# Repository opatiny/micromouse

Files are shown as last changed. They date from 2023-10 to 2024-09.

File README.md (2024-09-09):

# Algernon: A custom micromouse robot

YouTube demo of the project: https://youtu.be/nz4QlaSIkbY

Main repository for my bachelor's thesis project.

wholeMouse

## Related repositories

The software fo this robot can be found in the two following repositories:

- Software for the microcontroller: [opatiny/ms-software](https://github.com/opatiny/ms-software)
- TypeScript code for the debug web page (is then built and uploaded on the MCU): [opatiny/ms-webpage](https://github.com/opatiny/ms-webpage)

## Abstract

This project was inspired by the micromouse competitions, in which small autonomous maze-solving robots compete to solve an unknown maze in the shortest possible time. The main focus of the project was to design a micromouse from scratch, which implied electrical and mechanical design, as well as the manufacturing of our own custom PCB. A physical prototype of the robot was fully assembled and tested. The robot implements 5 ToF distance sensors, an accelerometer and two brushed DC motors with encoders. The microcontroller is an ESP32-S3, and a 2P1S LiPo battery is used as a power supply. On the software side, all of the sensors were tested independently and are functional. A basic odometry task was also implemented, which allows to track the robot's position, and speed regulation of the wheels was added. What is more, a remote debug interface using WiFi was programmed in order to visualize the robot's status in real time.

## Report of the project

The report of this thesis can be found in the `docs` folder of this repository: [bachelor-thesis-opatiny.pdf](./docs/bachelor-thesis-opatiny.pdf)

## Repository structure

These are the main folders in this repository:

- `docs`: All sorts of documentation about the project, as well as the datasheets and useful images of the components used.
- `electronics`: Contains all the KiCad files of the PCB.
- `mechanics`: All files related to mechanical design and manufacturing. Also contains all of our custom maze files.
- `matlab`: Calculations and plot realized during the project.
- `software`: Not the actual micro-controller software. This only contains a few tests done using the Micromouse Simulator tool.

## Software

All the software of the robot is in its own repository: [opatiny/ms-software](https://github.com/opatiny/micromouse).

## Electronic design

The robot's PCB was fully designed in KiCad. The list of all the components used can be found in [docs/electronics/mouseHardware.md](./docs/electronics/mouseHardware.md).

Render of the final PCB
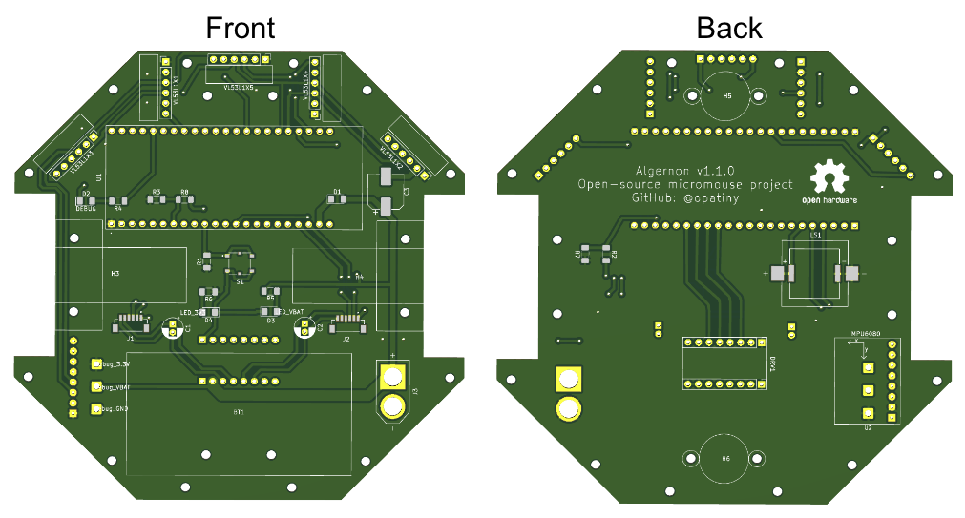
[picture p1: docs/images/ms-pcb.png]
pcb


3D view of the completed robot
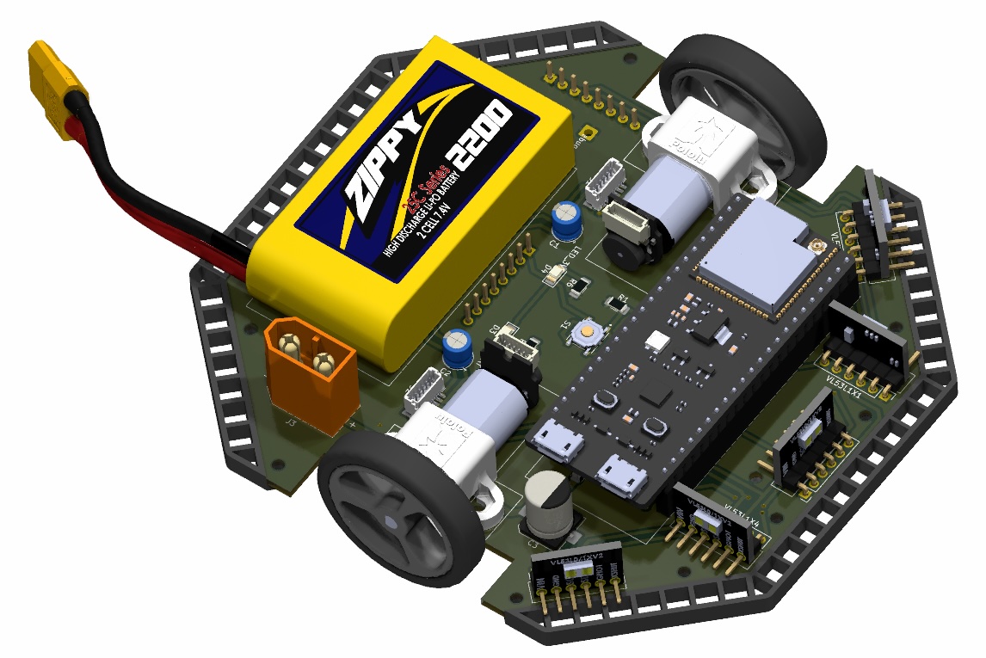
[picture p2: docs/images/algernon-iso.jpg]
3D


## Mechanical design

The mechanical design is relatively simple since the PCB is the main structural element. We just had to design our own caster wheel, that are 3D printed out of PETG, and custom bumpers, 3D printed out of flexible filament.

Comparison of commercial and custom caster wheel
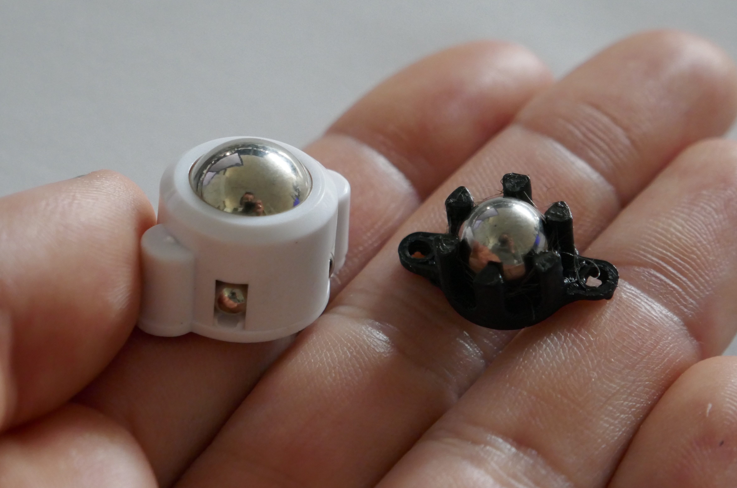
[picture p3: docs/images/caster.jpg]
caster


Close-up of the bumper
bumper

## Custom maze

In order to test our robot, we designed our own maze. The walls are 3mm MDF, spray painted white. The connectors are 3D printed out of PETG. Additional "bridge" parts are use to ensure the walls are parallel, and at the right distance from each other. All the parts were designed in solidworks.

The four types of connectors
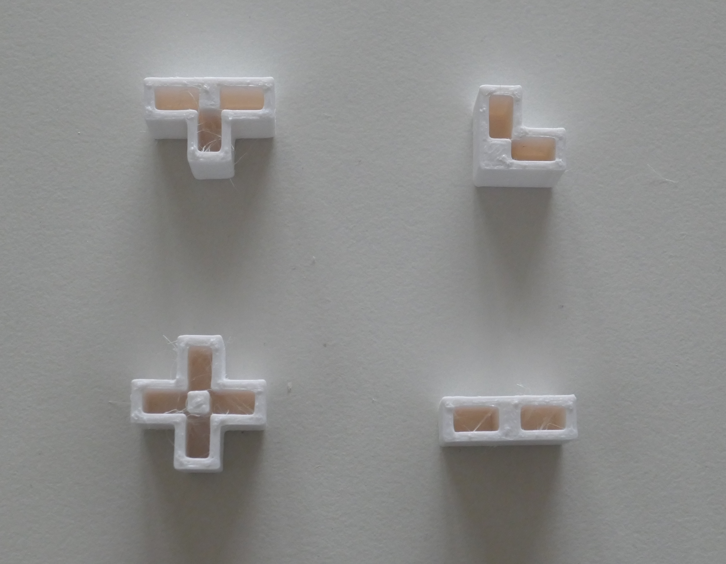
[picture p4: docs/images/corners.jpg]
connector


Example of a small section of maze, integrating one of the "bridge" parts
maze
bridge

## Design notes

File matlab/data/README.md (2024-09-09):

# Information about the data csv files

Motor speed absolute value from 0 to 255.

## Battery voltage when motors speed varies quickly

### `batteryVoltage1.csv`

- motor: 1
- motor speed: 200
- profile: rectangle
- length: 1 s
- sampling: 20 ms
- task priority: 0
- battery: 3S AAA batteries

### `batteryVoltage2.csv`

- motor: 1
- motor speed: 200
- profile: rectangle
- length: 1 s
- sampling: 5 ms
- task priority: 0
- battery: 3S AAA batteries

### `batteryVoltage3.csv`

- motor: 1
- motor speed: 200
- profile: rectangle
- length: 1 s
- sampling: 1 ms
- task priority: 2
- battery: 3S AAA batteries

### `batteryVoltage4.csv`

- motor: 1
- motor speed: 200
- profile: rectangle
- length: 1 s
- sampling: 5 ms
- task priority: 2
- battery: 3S AAA batteries

### `batteryVoltage4.csv`

- motor: 1
- motor speed: 100
- profile: rectangle
- length: 1 s
- sampling: 5 ms
- task priority: 2
- battery: LiPo battery 2S1P
- added 0.1uF ceramic capacitors on motor terminals

## Analyse distance sensors results

### `distanceSensorsConstant1.csv`

Using breadboard with 2 sensors to see what the measurements look like.

- constant distance of 250 mm from edge of board
- measurements every second using N times DELAY
- timing budget: 140 ms

### `distanceSensorsCalibration1.csv`

Using breadboard with 2 sensors to see what the measurements look like when distance varied.

- distance varied from 0 to 450 mm with 50mm steps (from edge of board)
- using the push button to measure when required
- timing budget: 140 ms

## Analyse encoders data

Log the data the encoder for a given speed profile. All measurements were made on motor 1.

### `encoders1.csv`

- profile: rectangle
- max speed: 100
- movement length: 1 s
- encoding: X4
- sampling: 5 ms

### `encoders2.csv`

- profile: trapeze
- ramp delay: 1
- max speed: 100
- movement length: 1 s
- encoding: X4
- sampling: 5 ms

### `encoders3.csv`

- profile: step response
- max speed: 100
- encoding: X4
- sampling: 5 ms

### `encoders4.csv`

- profile: trapeze
- ramp delay: 5
- max speed: 100
- movement length: 1 s
- encoding: X4
- sampling: 5 ms

### `encoders5.csv`

- profile: step response
- max speed: 255
- encoding: X4
- sampling: 5 ms

### `encoders6.csv`

- profile: trapeze
- ramp delay: 10
- max speed: 100
- movement length: 1 s
- encoding: X4
- sampling: 5 ms

## True wheel speed vs command

We want to analyse what the true wheel speed is depending on the duty cycle applied to the motor

- command (duty cycle) is a value between -256 and 255
- the actual motors speed is in rpm
- robot: Algernon v1.1.0
- motors 3 (left) and 4 (right)
- battery: LiPo battery 2S1P

### `wheelSpeedCalibration1.csv`

- delay between speed changes: 1s
- speed range: [0, 255]
- command step: 10

### `wheelSpeedCalibration2.csv`

- delay between speed changes: 2s
- speed range: [-255, 255]
- command step: 5

### `wheelSpeedCalibration3.csv`

- delay between speed changes: 1s
- speed range: [-255, 255]
- command step: 1

### `wheelSpeedCalibration5.csv`

- delay between speed changes: 1s
- speed range: [-255, 255]
- command step: 5

Caution: in this case we use the new speed measurement X/dt and the odometry delay is 1ms

## Wheel speed calibration

We use the same dataset types as for wheel speed calibration.

Check whether cpp and matlab yield to same result.

- command (duty cycle) is a value between -256 and 255
- robot: Algernon v1.1.0
- motors 3 (left) and 4 (right)
- battery: LiPo battery 2S1P

### `wheelSpeedCalibration4.csv` and `polynoms4.csv`

- delay between speed changes: 1s
- speed range: [-255, 255]
- command step: 5

### `wheelSpeedCalibration6.csv` and `polynoms6.csv`

- delay between speed changes: 1s
- speed range: [-255, 255]
- command step: 5

Caution: in this case we use the new speed measurement X/dt and the odometry delay is 1ms

## Test speed calibration

Verify if desired RPM speed and actual motor speed is the same.

- speed range: -550 -> 550 rpm
- robot: Algernon v1.1.0
- motors 3 (left) and 4 (right)
- battery: LiPo battery 2S1P

### `testSpeedCalibration1.csv`

- delay between speed changes: 1s
- speed step: 10 rpm

## Test PID

Check how the desired speed is reached by both wheels, using a PID regulator

- robot: Algernon v1.1.0
- motors 3 (left) and 4 (right)
- battery: LiPo battery 2S1P

## `testPid1.csv`

- Kp: 0.020
- Ki: 0.000
- Kd: 0.010

Time in ms.

## `testPid2.csv`

Completely refactored odometry to fix speed issues. Odometry and PID loops have a delay of 10 ms.

- Kp: 0.020
- Ki: 0.001
- Kd: 0.000

Time in seconds.

## `testPid3.csv`

- Kp: 0.020
- Ki: 0.000
- Kd: 0.001

Time in seconds.

## `testPid3.csv`

- Kp: 0.020
- Ki: 0.002
- Kd: 0.000

Time in seconds.

## `testPid6.csv`

- Kp: 0.015
- Ki: 0.003
- Kd: 0.000

## `testPid7.csv`

- Kp: 0.060
- Ki: 0.001
- Kd: 0.000

## Compare speed measurement methods

We measure the speed in 2 ways:

1. divide number of counts from since last call by the time elapsed
2. divide a known number of counts, always the same, by the time taken to move this nb of steps

- robot: Algernon v1.1.0
- motors 3 (left) and 4 (right)
- battery: LiPo battery 2S1P

### `compareSpeeds1.csv`

- odometry task delay: 10ms

```csv
 pNegLeft, pPosLeft, pNegRight, pPosRight
-0.0000000061, -0.0000000037, -0.0000000037, 0.0000000016
-0.0000052032, 0.0000054147, -0.0000028143, -0.0000009649
-0.0016165279, -0.0019280235, -0.0008025189, 0.0002857632
-0.0617476981, 0.2247056010, 0.0270471843, 0.0791166413
-42.7075095500, 74.9729712389, -45.3625414581, 45.1797983120
```

### `compareSpeeds2.csv`

- odometry task delay: 1ms
- same regressions as before
- we see that the speed speed is really big for smaller speeds: variations of 167 rpm at a time

Questions:

- why is the low speed never zero??

```csv
 pNegLeft, pPosLeft, pNegRight, pPosRight
-0.0000000061, -0.0000000037, -0.0000000037, 0.0000000016
-0.0000052032, 0.0000054147, -0.0000028143, -0.0000009649
-0.0016165279, -0.0019280235, -0.0008025189, 0.0002857632
-0.0617476981, 0.2247056010, 0.0270471843, 0.0791166413
-42.7075095500, 74.9729712389, -45.3625414581, 45.1797983120
```

### `compareSpeeds4.csv`

- odometry task delay: 1ms
- logging delay: 250 ms
- both high speed and low speed are computed every 1ms

## Controller delay impact

We have a delay in the `robotDriveStraight` function, that implements the speed controllers of the wheels. We vary this delay in order to see the impact on the step response of the controller. Ideally, we want to reduce this delay to the maximum, because delay in regulation loops lead to higher instability of the system.

- target speed: 200 rpm
- robot: Algernon v1.1.0
- motors 3 (left)
- battery: LiPo battery 2S1P

Files: `controllerDelayImpactXXms.csv`

## Analyse commands

Goal: see how much the command is increased over time in order to achieve desired speed in givn time.

## Max robot acceleration

Measuring the true maximal acceleration of the robot.

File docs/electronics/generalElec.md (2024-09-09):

# Components and features of the PCB

What do we want on our mouse?

- 2x DC motors with encoders
- 1x H bridge dual motor driver
- 1x MPU with bluetooth and/or wifi for debug
- 1x buzzer for sound signals
- debug LEDS
- 5x distance sensors
- battery
- accelerometer

The following sections include information on how the different elements work, and how we implemented them on the PCB. The list of the exact components used can be found in [mouseHardware.md](./mouseHardware.md).

## Distance sensors: VL53L1X

The device pins have the following functions:
[!](../datasheets/images/vl53l1x-pin-description.png)

- The `XSHUT` pin has to be pulled up for the device to be active.
- Device default address is 0x29 (41)
- Arduino library: Adafruit VL53L1X
- range: ~30 to 4000 mm -> the smallest distance is not great for our use case...
- timing budget: from 20 to 1000ms. Be careful, if the timing budget is too short, the whole MCU reboots. It basically defines how long a measurement can be.
  "140 ms is the timing budget which allows the maximum distance of 4 m (in the dark on a white chart) to be reached under Long distance mode Increasing the timing budget increases the maximum distance the device can range and improves the repeatability error. However, average power consumption augments accordingly." - https://xod.io/
- We can't change the I2C addresses permanently on the VL53L1X!!! https://community.st.com/t5/mems-sensors/vl53l1x-device-address-storage/td-p/355584
- we'll therefore need an I2C to GPIO module because otherwise we don't have enough pins on our MCU

- minimum timing budget: https://forum.pololu.com/t/vl53l1x-minimum-timing-budget/20485

## Buzzer

We'll need PWM to get different notes with the buzzer.
"All GPIO pins on XIAO ESP32S3 support PWM output. Therefore, you can use any pin to output PWM to adjust the brightness of lights, control servos, and other functions." - https://wiki.seeedstudio.com/xiao_esp32s3_pin_multiplexing/

The buzzer takes a frequency of typically 400kHz, how do we generate this? This is actually not true. You apply the frequency that you want to hear, so i.e. 440 Hz.

## Debug LEDs

We want to put a bunch of debug LEDs in the circuit.

- high power (from battery)
- 3.3V at voltage regulator output

## Battery voltage measurement

We want to add a voltage divider on the battery in order to measure the battery voltage and hence know when the battery is discharged. This requires reading an analog voltage -> ADC.

## Encoders

- we use an interrupt with a small routine that increases/decreases a counter depending on the spin direction

## Access ESP USB connector

Since it's very compact, we need USB angled connectors.

The connectors we bought are 18 x 13 x 7 mm.

## Final PCB v1.0.0

Dimensions: 110x110mm

Possible issues:

- add capas to decouple power lines near to important components (MCU, sensors)
- are we using the USB pins as GPIO and they would need to be reconfigured?
- do the murata buzzers work as expected?

## Links

- adafruit guide: https://learn.adafruit.com/adafruit-vl53l1x?view=all
- https://github.com/pololu/vl53l1x-arduino?utm_source=platformio&utm_medium=piohome
- timing budget reference: https://xod.io/libs/wayland/vl53l1x-time-of-flight/set-measurement-timing-budget/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,ms%20up%20to%201000%20ms.&text=20%20ms%20is%20the%20minimum,only%20in%20Short%20distance%20mode.&text=33%20ms%20is%20the%20minimum,work%20for%20all%20distance%20modes.

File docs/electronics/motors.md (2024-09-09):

# Motors and encoders

We are using brushed DC motors with an integrated gearbox. Additionally, we measure the motors movement with magnetic encoders.

## Voltage drop due to motors

"One major drawback to working with motors is the large amounts of electrical noise they produce. This noise can interfere with your sensors and can even impair your microcontroller by causing voltage dips on your regulated power line. Large enough voltage dips can corrupt the data in microcontroller registers or cause the microcontroller to reset." - https://www.pololu.com/docs/0J15/9

**Solution:** Solder 0.1uF ceramic capacitors (not polarized!) between motor terminals and motor case

## Cables

The Polulu motors encoders are equipped with JST SH cables. Two of the 6 pins are directly connected to the motors pins. By checking the specifications, we wee that the cables are 28AWG, which can have a maximal continuous current of 1.5A.

- http://www.mosaic-industries.com/embedded-systems/electronic-instrument-design-new-product-development/cables/ribbon-cable-current-rating
- https://www.pololu.com/product/4763/specs

## Non-linear motor speed VS PWM command

Is probably caused by the driver!! Other people had very similar results

- https://forum.pololu.com/t/nonlinear-relatioonship-between-motor-encoder-speed-and-pwm/20092/7
- change the PWM frequency!!! https://forum.pololu.com/t/drv8835-non-linear-current-draw-vs-pwm-duty-cycle/8430/4 -> around 20kHz

- could also be improved by using either coast mode (fast decay) or brake mode (slow decay). According to the previous link, brake mode would be the best. See the drivers datasheet (page 9) for how to use one mode or the other.

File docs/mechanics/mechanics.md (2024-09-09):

# Mechanical parts of the micromouse

## PCB: The main structural element

## Custom caster wheels

- M2 screw head between 3.3 and 3.5mm

- these caster wheels by polulu would have worked, they're only 10mm high: https://www.pololu.com/product/951

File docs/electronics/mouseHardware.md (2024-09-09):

# Algernon: The hardware

## Micro-controller

- Reference: ESP32-S3-DevKitC-1U-N8R8
- Manufacturer: Espressif
- Flash: 8 Mb
- RAM: 8 Mb
- CPU frequency: up to 240MHz
- SPI clock frequency: max 80 MHz by default
- Wireless: WiFi and Bluetooth
- Board dimensions: 63 x 25 mm
- Link: https://www.mouser.de/ProductDetail/356-32S3DEVKTC1UN8R8

## Motors

- Reference: 30:1 Micro Metal Gearmotor HPCB 12V with Extended Motor Shaft
- Manufacturer: Polulu
- Voltage: 12V
- Gearbox ratio: 30:1
- Exact gearbox ratio: 29.861:1
- No-load: 1100 rpm, 0.08 A
- Stall: 38 mNm, 0.75 A
- Max power: 1.1 W
- Link: https://www.pololu.com/product/3049

## Motors driver

- Reference: DRV8833 Dual Motor Driver Carrier
- Manufacturer: Polulu
- Current: max 1.5 Arms output per motor
- Operating voltage (motor): 2.7 to 10.8 V
- Current control max frequency $f_{PWM}$: 50 kHz
- Board dimensions: 20 x 13 mm
- Link: https://www.pololu.com/product/2130

## Encoders

- Reference: Magnetic Encoder Pair Kit with Side-Entry Connector for Micro Metal Gearmotors
- Counts per revolution: 12 CPR
- Input voltage: 2.7-18V
- Connectors: 6-pin female JST SH-type
- Link: https://www.pololu.com/product/4761

## Distance sensors

- Reference: VL53L1X Time-of-Flight ToF Distance Sensor
- Manufacturer: TinyTronics
- Range: 30-4000 mm
- Communication: I2C
- Supply voltage: 3.3-5V
- Board dimensions: 25x10.7 mm
- Link: https://www.tinytronics.nl/en/sensors/distance/vl53l1x-time-of-flight-tof-distance-sensor

## Accelerometer

- Reference: MPU6050
- Manufacturer: InveSense
- Communication: I2C
- Features: 3 axis accelerometer and 3 axis gyroscope
- Supply voltage: 2.4-3.5V
- Board dimensions: 21x15.5 mm
- Link: https://invensense.tdk.com/wp-content/uploads/2015/02/MPU-6000-Datasheet1.pdf

## Battery

- Reference: RD XT 1100 S2
- Manufacturer: Red Power
- Chemistry: Lithium polymer
- Capacity: 1100 mAh
- Configuration: 2S1P
- Nominal voltage: 7.4 V
- Maximum output continuous current: 27 A
- Connector: XT60
- Dimensions: 55 x 30 x 17mm
- Link: https://www.reichelt.de/dk/en/li-po-battery-7-4-v-1100-mah-rd-xt-1100-s2-p336956.html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

## Buzzer

- Reference: PKLCS1212E20A0-R1
- Manufacturer: Murata
- Technology: piezo-electric
- Link: https://www.mouser.de/ProductDetail/Murata-Electronics/PKLCS1212E20A0-R1?qs=qEIx2DuoqD%2FARxhlKJ5jbw%3D%3D

## Push button

- Reference: PTS526 SMG15 SMTR2 LFS
- Manufacturer: C&K Switches
- Dimensions: 6.4x5.2mm
- Link: https://www.mouser.de/ProductDetail/611-PTS526SMG15SMR2L

## Wheels

- Reference: Pololu Wheel 32×7mm
- Manufacturer: Polulu
- Tires material: Silicone
- Link: https://www.pololu.com/product/1087

## Other

- schottky: NSR0320MW2T1G (20V, 1A)

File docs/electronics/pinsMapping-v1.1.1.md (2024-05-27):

# Pins mapping of the ESP32-S3-DEVKITC (Espressif) - PCB v1.1.0

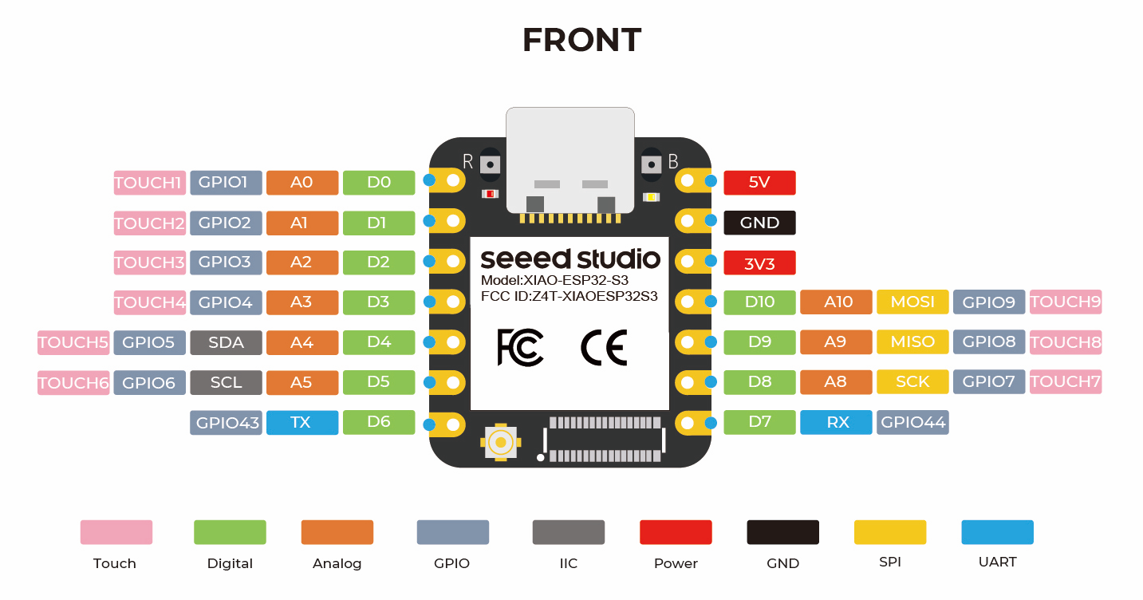
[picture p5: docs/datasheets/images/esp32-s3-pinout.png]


## Left side (USB connectors at the bottom)

| Jumper pin | Silk label | Pin value | Usage |
| --- | --- | --- | --- |
| J1_1 | 3V3 | 3V3 | MCU output voltage (Vin) |
| J1_2 | 3V3 | 3V3 | MCU output voltage (Vin) |
| J1_3 | RST | RST | |
| J1_4 | 4 | GPIO4 | Encoder left, pin 1 |
| J1_5 | 5 | GPIO5 | Encoder left, pin 2 |
| J1_6 | 6 | GPIO6 | Buzzer |
| J1_7 | 7 | GPIO7 | MCU 3.3V measurement (VCC) -> ADC2_4 |
| J1_8 | 15 | GPIO15 | |
| J1_9 | 16 | GPIO16 | |
| J1_10 | 17 | GPIO17 | Push button |
| J1_11 | 18 | GPIO18 | |
| J1_12 | 8 | GPIO8 | |
| J1_13 | 3 | GPIO3 | Battery voltage measurement (ADC1_2) |
| J1_14 | 46 | GPIO46 | Left motor, pin 1 |
| J1_15 | 9 | GPIO9 | Left motor, pin 2 |
| J1_16 | 10 | GPIO10 | Right motor, pin 2 |
| J1_17 | 11 | GPIO11 | Right motor, pin 1 |
| J1_18 | 12 | GPIO12 | |
| J1_19 | 13 | GPIO13 | Encoder right, pin 1 |
| J1_20 | 14 | GPIO14 | Encoder right, pin 2 |
| J1_21 | 5V | 5V0 | Connected to battery through schottky diode |
| J1_22 | G | GND | Common ground |

## Right side (USB connectors at the bottom)

Note: ToF are VL53L1X time of flight distance sensors.

| Jumper pin | Silk label | Pin name | Usage |
| --- | --- | --- | --- |
| J3_1 | G | GND | Common ground |
| J3_2 | TX | GPIO43 | |
| J3_3 | RX | GPIO44 | |
| J3_4 | 1 | GPIO1 | |
| J3_5 | 2 | GPIO2 | Blink debug LED |
| J3_6 | 42 | GPIO42 | |
| J3_7 | 41 | GPIO41 | |
| J3_8 | 40 | GPIO40 | Left ToF XSHUT |
| J3_9 | 39 | GPIO39 | Front-left ToF XSHUT |
| J3_10 | 38 | GPIO38 | Not usable (RGB LED)!! |
| J3_11 | 37 | GPIO37 | Not usable (memory)!! |
| J3_12 | 26 | GPIO36 | Not usable (memory)!! |
| J3_13 | 35 | GPIO35 | Not usable (memory)!! |
| J3_14 | 0 | GPIO0 | Front ToF XSHUT (Needs some time before used as GPIO -> used for boot) |
| J3_15 | 45 | GPIO45 | |
| J3_16 | 48 | GPIO48 | |
| J3_17 | 47 | GPIO47 | SDA |
| J3_18 | 21 | GPIO21 | SCL |
| J3_19 | 20 | GPIO20 | Front-right ToF XSHUT |
| J3_20 | 19 | GPIO19 | Right ToF XSHUT ^ |
| J3_21 | G | GND | Common ground |
| J3_22 | G | GND | Common ground |

- "For boards with **Octal SPI** flash/PSRAM memory embedded **ESP32-S3-WROOM-1/1U** modules, and boards with ESP32-S3-WROOM-2 modules, the **pins GPIO35, GPIO36 and GPIO37** are used for the internal communication between ESP32-S3 and SPI flash/PSRAM memory, thus **not available for external use**." - https://docs.espressif.com/projects/esp-idf/en/stable/esp32s3/hw-reference/esp32s3/user-guide-devkitc-1.html

## Other

- RGB LED on pin 38

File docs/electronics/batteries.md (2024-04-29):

# Batteries and battery charger

## Batteries: 1100mAh 2S1P LiPo batteries

- 7.4V
- length 55mm
- connector: XT60 like for drones
- max current: 27A
- weight: 55g
- capacity: 1.1Ah

What is balancing and how to deal with it?

- the battery has 2 connectors
- "Balancing plug. It's used to equalize the charge between the pack's cells when you recharge the LiPo."
- still need to find a charger

## Charger: 608AC smart charger

To charge our batteries:

- plug charger
- connect batteries: the voltage in each cell appears
- set Task to Charge
- set Chemistry to LiPo
  set Condition to the voltage at which you want to charge each of the cells, e.g 4.1 (max for our cells would be 4.2V)
- set Cells to 2S
  Set the charging current to

## Important notice for LiPo batteries

- do not discharge batteries more than 70% of nominal capacity (draw max 700mAh from a 1000mAh battery)
- never let voltage of the cells drop below 2.6V -> in our case we must get a warning when voltage is approaching 5.2V
- our battery current should not exceed 1C -> do not charge with more than 1.1 A!!

## Micromouse power consumption

Power consumption of the different elements of the mouse:

- ESP32: we estimate at around 300 mA
  - note: wifi can use up to 300mA
- Motors: max 0.75 A per motor
- Distance sensors: 16-18 mA when ranging
- Accelerometer: ~4mA max
- Encoders: operating supply current max 3.5 mA per hall effect sensor
- Motors driver: 1.7 - 3 mA

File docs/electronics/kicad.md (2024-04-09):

# Notes on the design of the PCB in KiCad

## Layout

- whenever placing mechanical component (motors, holes), a grid in mm is used (the biggest possible)
- for electronics components, a grid in mils is used, starting with 25 mils

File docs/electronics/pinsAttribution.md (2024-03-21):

# Pins attribution of the ESP32-S3



| Pin | Usage |
| --- | --- |
| D0  | Encoder left, pin 1 |
| D1  | Encoder left, pin 2 |
| D2  | Encoder right, pin 1 |
| D3  | Encoder right, pin 2 |
| D4  | SDA |
| D5  | SCL |
| D6  | Voltage divider battery |
| D7  | Left motor, pin 1 |
| D8  | Left motor, pin 1 |
| D9  | Right motor, pin 1 |
| D10 | Right motor, pin 2 |
| 5V  | Not connected |
| GND | Common ground |
| 3V3 | MCU input voltage |

## Pins attribution of GPIO expander

- 5x distance sensor XSHUT pin (OUTPUT)
- 1x buzzer
- RGB LEDs?

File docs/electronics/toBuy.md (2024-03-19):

# List of things to buy

## Polulu

- 4x motors (I bought the slightly less powerful 12V ones): https://thepihut.com/products/micro-metal-geared-motor-w-encoder-6v-530rpm-30-1
- 2x dual motor drivers: https://www.pololu.com/product/2130
- 2x set of silicon wheels 32mm diameter: https://www.pololu.com/product/1087/specs
- 2x speed controller?: https://www.pololu.com/product/3142 -> USELESS!

## Tiny electonics

11.03.2024

- distance sensors: https://www.tinytronics.nl/en/sensors/distance/vl53l1x-time-of-flight-tof-distance-sensor

## Amazon

19.03.2024

- Lipo battery charger: ISDT 608AC Battgo Lipo Battery Charger

## Reichelt

19.03.2024

- 4x lipo battery: https://www.reichelt.de/akku-pack-li-polymer-7-4-v-1100-mah-rd-xt-1100-s2-p336956.html?&trstct=pol_8&nbc=1

## other

- jst sh 6 pins cables and connectors (for encoders)
- I2C to GPIO expander

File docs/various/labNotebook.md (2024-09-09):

# Lab notebook: daily project notes

## February

### 26 - 03

- order polulu components
- planning v1
- recapitulative state of the art table
- mms discovery and first test
- choice of MCU: esp32c3 and attribution of all pins
- configuration of programming environment of the esp32c3 on the mac
  - test of serial communication
  - first i2c device (accelerometer)
  - configure wifi

## March

### 04 - 10

- ordered distance sensors on tinyelectronics.nl

### 08 - 14

- received distance sensors
- started distance sensing thread and tried modifying the sensors I2C addresses
- realized that we cannot change the addresses permanently -> we'll have to do it every time the device is powered -> not enough pins -> need IO expander ove I2C

### 15 - 22

- try to find suitable battery
- order lipo batteries as well as charger
- made first motor tests with motor driver -> can make motor spin at various speeds
- use IO pins of the MCU on XSHUT pins to enhance distance sensors thread and have 2 sensors work in parallel
- after discussion, realized that it is probably easier to change the MCU board instead of adding IO expander. We're considering the Espressif ESP32-S3 board: the code will be the same, but we'll have more GPIO

### 25 - 31

- ordered JST and XT60 connectors on amazon
- ordered new esp boards on Mouser
- fixed distance sensors thread -> it now works with 2 sensors in parallel
- meeting Prof. Weiss on Monday
- battery voltage measurement task works

## April

### 01 - 07

- buzzer task works
- received batteries and charger and learned to use it
- manage to spin a motor forwards and backwards
- analysed impact of motor on battery voltage
- start encoder task -> problem: counter increases even when motor does not spin
- PCB v 0.1 schematic mainly finished
- started PCB layout too

### 08 - 14

- ordered ball bearings set on polulu for custom caster wheel cause the ones we have are to high
- finished finding footprints and 3D models for kicad
- model most of 3D parts in solidworks
- push button task
- X1 encoder task works but not X4 yet (will have 4x greater resolution, counting all edge changes)
- PCB layout mostly finished and asked for review from chevallier

### 15 - 21

- no news from chevallier
- finished PCB v1.0.0 and ordered on PCBway!
- globally finished report state of the art
- design and print springy bumper
- asked for access to a workshop but didn't actually get it
- create calibration procedure for distance sensors using button -> measured sensors data to see how it looks

### 22-28

- problems with custom clearance of the PCBs delayed delivery
- managed to make X4 encoding work
- worked on motor control
  - can go forward and backward at desired speed with ramp
  - can move N degrees
- finally received PCBs on saturday!

### 29 - 05

- long week this week, one of the downs of the project...
- assembly of PCB v1.0.0 on monday
- a lot of problems with switching to the new MCU, but managed to debug all of them by the end of the week
- corrected kicad for next version of PCB
- managed to make all threads work on Algernon except motors
- next monday: double check the new PCB and order on Aisler

## May

### 06 - 12

- on Monday, verified PCB and ordered 3 on Aisler
- didn't work on Algernon the rest of the week (ascention)
- except worked a bit on the report introduction

### 13 - 19

- fixed V1.0.0 problem with motor pin on same pins as RGB LED
- both motors work separately
- started writing code to control the robot movement
- question: should I refactor the code to use classes instead of having a global state object shared between function?
- received PCB V1.1.0 and assembled it
- list of expenses of the project
- programmed robot to stop when obstacle detected -> it moved for the first time!!
- start odometry task
- hardware is finished!! -> 2 weeks earlier than planned

### 20 - 26

- 2 days were holidays so worked a bit less
- add debug mode to log true rpm speed depending on speed command
- write PID control function
- worked on function to drive robot straight using pid on wheels speed

### 27 - 02

- worked a bit on report intro

## June

### 03 - 09

- work on motor speed calibration: convert a given speed in rpm to a command for the PWM
- worked on report theory and hadware parts

### 10 - 16

- worked on PID of the speeds of the two wheels in order to try to drive straight. Managed to have plots of the response of the controller that look relatively good. We have a problem with the speed measurement though, because it has very big steps -> not very precise
- Called Chevallier and we discussed of a way to improve the speed. 2 possibilites:
  - use timer and constant nb of steps. This will be more precise for low speeds
- use the induced voltage of the motor, that is proportional to its speed -> we will need voltage dividers and ADCs
- todo: speed vs induced voltage curve of the motors to determine the speed constant

### 17 - 23

Current state and goals until the end of the project?

Current state

- robot hardware works except for minor unimportant bugs
- all elements work separately and can be controlled though the serial interface
- PID on wheels speeds starts to work, robot moved straight for the first time

**Objectives until the end of the project**

1. implement the low speed measurement of the speed using a known nb of steps divided by delta t and compare both speeds
2. test the motors: speed vs induced voltage plot and deduce speed constant
3. try to measure motors speed through induced voltage
4. **important**: PID on the robot speed (v and omega) and add the walls term in order to stay in the middle of a corridor
5. wifi debug interface
   - retrieve state in the web page
   - be able to send commands to the robot to control it from the web page
   - plot interesting things: distances, controller data (speeds, commands, target)
6. write a good report

Chevallier approved.

- implemented new speed X/dt -> better than before, can update speed every 1 ms instead of every 10ms
- made wifi work for the first time in germany and managed to change serial params through it

### 24 - 30

- started working fully on graphical interface
  - export important data from robot and send them over wifi
  - use react components to display the information
- managed to plot robot distances irl, there is a problem with the messages queue, sometimes big delays between two messages
- plot the robot position in an x/y plane!
- worked on robot speed control, where the regulation is made on v and omega of the robot

## July

### 01 - 07

- continued with the graphical interface and the plot of the regulators
- started working a lot on the report: wrote maze, mechanics and solutions chapters

### 08 - 14

Exams

### 15 - 21

Exams

### 22 - 28

- working full time on the report

### 29 - 04

- finished electronics part
- enhanced and reorganised docs in the ms-software repo
- made tests to plot motor speed VS voltage using a DC power supply
- wrote abstract and acknowledgements
- made a lot of progress on the debug interface: the commands and wheel speeds plots work
- added the command box to submit commands through wifi
- learned to build the code to put in on the micromouse
- debug interface is pretty much finished

## August

## 05 - 11

- added schematics to theory chapter
- worked on software chapter
- enhanced serial menu and added `m` utilities
- finished results chapter
- enhances repositories documentation
- wrote conclusion chapter

## 12 - 18

- correct report after supervisor's feedback
- printed thesis

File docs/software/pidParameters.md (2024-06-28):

# Choosing PID parameters

We proceed by trial and error.

## Wheels speed PID

Both wheels have the same PID parameters. The speed regulated is in rpm.
Rolled really straight for about 7m.

- (BA) Kp: 0.100
- (BB) Ki: 0.001
- (BC) Kd: 0.004

## Robot speed PID

We regulate the robot's speed using two PID regulators, one for the angular speed (in rad/s) and the other one for the linear speed (in m/s).

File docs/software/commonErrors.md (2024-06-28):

# Common programming errors and possible causes

Errors of the microcontroller

## Core 1 panic'ed

### not enough stack

The core panics which causes the device to reboot all of the time. This error is generally related to the multiple threads running in parallel. We identified two main causes:

1. No `vTaskDelay` in the `while` loop: without a delay in the loop the hand can never be given to the other tasks, which causes the device to crash.
2. Insufficient stack size of the task: If the tasks takes more memory than it was allocated it generate a stack overflow which crashes the device.

### `DoubleException`

https://www.esp32.com/viewtopic.php?t=27538

"A Double Exception is the result of an exception occurring within the exception handler, and might be expected to be the result of insufficient stack, or stack corruption."

In my case migrating 2 threads to core 0 solved the issue.

**Hypothesis:** the total available stack was filled because they were too many threads.

### `IntegerDivideByZero`

Happens when an integer is divided by zero somewhere in the code. The question is: how do we detect where that happens?

Disable all tasks on by one until you find the one(s) responsible for the error. Dig into the functions until you find where the problematic division happens.

### `LoadProhibited`

### `Interrupt wdt timeout on CPU1`

Happens when interrupt subroutine take to long to execute, typically if some `Serial.print` are done inside of it...

## `E (4917) gpio: gpio_install_isr_service(450): GPIO isr service already installed`

## `A fatal error occurred: Failed to connect to ESP32-S3: No serial data received.`

The serial device is not detected.

- check the list of available serial devices with `ls /dev/tty.*`
- check that the cable is both for charging and transfering data!
- check that the correct USB connector is used if they are 2

## Serial monitor prints unknown characters

Probably a problem with the serial speed. Add following lines to `platformio.init` and check the given speeds are correct:

```
monitor_speed = 115200
upload_speed = 921600
```

## `E (4478) SPIFFS: mount failed, -10025`

Issue on the espressif devkit. Probably because partition was never formatted. Try uploading the contents of the `data` folder on the MCU with

```bash
pio run --target uploadfs
```

## `ERROR: Too many messages queued`

Happens when the MCU sends too many messages / too long messages too frequently and it can't keep up with the rate

https://github.com/me-no-dev/ESPAsyncWebServer/issues/504

## Links

- espressif serial comm problems: https://forum.digikey.com/t/esp32-s3-devkitc-1u-cant-get-serial-monitor-to-work/28069/2

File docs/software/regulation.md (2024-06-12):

# Coding your own regulators

The micromouse requires mutliple regulators to work as expected:

- speed regulation of the DC motors based on encoder values
- position regulation to follow a desired trajectory based on distance sensor readings

In this document, we sumarize multiple ressources to code your own regulator and find the correct values of the different parameters.

## Motors control by coding a PD regulator yourself

Designing a PD controller for micromouse: https://www.youtube.com/watch?v=qKoPRacXk9Q

Corresponding github repository: https://github.com/ukmars/motorlab

- voltage => speed
- current => torque => acceleration

Steps:

- plot speed VS time for different constant voltages (open loop) -> you should put a wheel on the motor with similar inertia to the robot
- deduce the gain $K_m$ of the system by plotting end values
- compute the time constant by drawing the tangent at the origin of the curve
- in a PD controller, you have two parameters to optimize : Kd and Kp. The goal is to have a voltage in the motors that is close to the voltage predicted by the feed forward. If the voltage in the motors is saturating and is oscillating between max and min voltage, it's really bad for the motors! Your controller is therefore not necessarily good even though the speed response and the displacement look really good! That's why you should always look at the command sent to the motors
- there is a relationship between Kd and Kp and $\zeta$and $\omega_n$.

- $\zeta$: dampening factor
- $\omega_n$: bandwidth

## Anti windup

## PID theory

- P: proportional term, corrects present error
- I: integral term, corrects past error
- D: differential term, corrects future error

## Phase lead controller: an alternative to PID or PD

- https://micromouseonline.com/2011/05/16/designing-a-phase-lead-controller/

## Wall and line tracking for micromouse

Peter Harrison: https://www.youtube.com/watch?v=22l6MrAwN-o

- two types of errors: offset and angle errors, and they can be combined! but you don't see that based on the sensors!!
- line following and wall following are the same problem
- how to correct this?
  - the robot is constrained: it cannot move sideways
  - we need a feedback system with a controller
  - prior art: everyone says use a PID controller
  - PH: a PD controller is enough
  - we measure an error but we don't know if its angle or offset
  - the D term acts on the rate of change -> the $\Delta t$ is critical
- inputs and outputs of a robot
  - inputs: v and omega
  - output: x,y,theta

"The position of the wheels is controlled using an encoder for feedback, this allows them to turn at the same speed, you can't just feed the motors with the same voltage or PWM and expect it to go in a straight line. A separate controller for forward and rotational movement is mixed and then sent to the motors."

What we take out of this:

- we first have to implement a controller that makes both wheels spin at the same speed when we want them to
- then add another controller for the wall following and combine both

## Links

- visual explanation of PID regulator: https://www.youtube.com/watch?v=4Y7zG48uHRo
- PID equation IEEE course: https://docs.google.com/presentation/d/19loBpku__17k4MO-2T24BOqiYk6qPrbNBHbNcyRvOSU/edit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
- example of bdc motor on esp32 s3 with PID!!! https://github.com/espressif/esp-idf/tree/v4.4/examples/peripherals/mcpwm/mcpwm_brushed_dc_control
- SP-IDF is the official development framework for the ESP32: https://docs.espressif.com/projects/esp-idf/en/stable/esp32/index.html
- https://micromouseonline.com/2011/05/15/designing-the-motor-controller/
- PID code example: https://github.com/MattFach/Micromouse/blob/master/test/PID%20control.c

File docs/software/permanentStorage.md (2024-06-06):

# Storing variables permanently in flash

https://randomnerdtutorials.com/esp32-save-data-permanently-preferences/

https://community.platformio.org/t/preferences-not-working-with-esp32-s2-and-platformio-but-working-with-arduino-ide/25938

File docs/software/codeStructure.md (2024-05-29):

# Multitasking

## Using multiple tasks

We use freertos to run multiple tasks in parallel.

## Questions

- what are semaphores and how to use them?
- what are queues and how to use them?
- is there a max number of threads?
- how to use both cores?

## Tasks priorities

https://www.freertos.org/RTOS-task-priority.html

## Using both cores

Assign tasks either to core 0 or 1.

```cpp
void taskRobotMove() {
  xTaskCreatePinnedToCore(TaskRobotMove, "TaskRobotMove", 4096, NULL,
                          3, NULL, 0);  // attached on core 0!!
}
```

## Links

- discussion on multitasking: https://www.esp32.com/viewtopic.php?t=8944
- tasks and co-routines: https://www.freertos.org/taskandcr.html
- freertos docs: https://www.freertos.org/a00125.html
- round robin scheduling: https://en.wikipedia.org/wiki/Round-robin_scheduling#:~:text=Round%2Drobin%20(RR)%20is,also%20known%20as%20cyclic%20executive).
- microseconds delay in freertos: https://www.freertos.org/FreeRTOS_Support_Forum_Archive/December_2014/freertos_Microsecond_delay_within_task_edfcdf0fj.html

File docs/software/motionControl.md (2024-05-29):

# Control of the mouse movement

They are many challenges we have to face:

- drive straight: be able to remain in the center of a corridor
- turn left and right to navigate through the maze
- follow a known path
- handle diagonals?

"Remember that your main aim is position control rather than velocity control. Your software will adjust motor speeds to achieve a given mouse position. There is a likely to be a tradeoff between good positional control and high speed – even before you get to the stage of skidding out of control on the corners." - https://micromouseonline.com/micromouse-book/sensors/odometry/

## Control of one motor

We first want to be able to control one motor. If we are able to give a speed to a motor and a distance for which it has to spin at that speed, the control of the whole robot will be a lot easier.

## Control of both motors together

Controlling the speeds of the two motors at the same time is what will allow us to make the mouse follow a desired trajectory. Ideally, at a higher level, we would like to give complex commands to the mouse such as "go forward 10 cm" and have then not have to worry about it anymore.

We can define a set of basic moves we would like the mouse to do

- go forward a given distance
- go backwards a given distance
- turn on the spot of xx degrees, negative values could be clockwise and positive anti-clockwise
- turn of xx degrees with a given radius?

## Problem with structuring the code

I initially structured the code in order to have a main `state` object passed to all the functions that need it in the different tasks. Indeed, since all tasks run in parallel, I find it difficult to see how I can keep multitasking while using classes. Using classes would probably make the final interface easier, and it would therefore be a more elegant solution, but I don't see how to implement it right now.

- example odometry code and robot simulator: https://www.toptal.com/robotics/programming-a-robot-an-introductory-tutorial
- concurrent planning and execution: https://www.cs.cmu.edu/~reids/papers/tca-ambler.pdf

## Links

- wheel slipping issue: https://robotics.stackexchange.com/questions/1658/implementing-slip-compensation-into-a-half-size-micromouse
- reading encoder data on arduino: https://github.com/ukmars/ukmarsbot/blob/master/docs/encoder-software.md
- types of errors in the mouse position (I should have used steppers -> much less errors): https://micromouseonline.com/micromouse-book/navigation/straights/
- UCBE course: https://ieee.berkeley.edu/micromouse-lab-5/

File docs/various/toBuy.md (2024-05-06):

# List of orders done for the project

## Polulu

- 4x motors (I bought the slightly less powerful 12V ones): https://thepihut.com/products/micro-metal-geared-motor-w-encoder-6v-530rpm-30-1
- 2x dual motor drivers: https://www.pololu.com/product/2130
- 2x set of silicon wheels 32mm diameter: https://www.pololu.com/product/1087/specs
- 2x speed controller?: https://www.pololu.com/product/3142 -> USELESS!

Polulu order 2: 2024.05.06

Motors, drivers, jst cables, wheels and brackets.

## Tiny electonics

11.03.2024

- distance sensors: https://www.tinytronics.nl/en/sensors/distance/vl53l1x-time-of-flight-tof-distance-sensor

## Amazon

19.03.2024

- Lipo battery charger: ISDT 608AC Battgo Lipo Battery Charger

  25.03.2024

- XT60 connectors
- JST SH 6 pins surface mount connectors

  10.04.2024

- set of ball bearings (for custom caster wheel)

- XT60 connectors
- JST SH connectors

- resistors book
- ceramic capacitors set
- electrolytic capacitors set

  2024.05.06

- tweezers
- m2x8mm screws

## Reichelt

19.03.2024

- 4x lipo battery: https://www.reichelt.de/akku-pack-li-polymer-7-4-v-1100-mah-rd-xt-1100-s2-p336956.html?&trstct=pol_8&nbc=1

  03.05.2024

- 50 x NSR0320MW2T1G Schottkydiode, 20 V, 1 A, SOD-323

## Exp Tech

2024.03.22

- jst sh 6 pins cables female-female and board with big pins

## Mouser

25.023.2024

- smaller buzzers Murata
- push buttons (smd and through hole for debug)
- new esp32-s3 boards by espressif

## other

- jst sh connectors (for encoders)
  - mouser (not in stock ;^;): https://www.mouser.de/ProductDetail/SparkFun/GPS-00579?qs=WyAARYrbSnYMUvZSImI8yA%3D%3D
- XT60 connectors

  - mouser: https://www.mouser.de/ProductDetail/SparkFun/PRT-10474?qs=WyAARYrbSnYJaRDMiD9g2w%3D%3D
  - less expensive on amazon

- smaller buzzers
- push buttons (smd and through hole for debug)
  - through hole: https://www.mouser.de/ProductDetail/TE-Connectivity-PB/FSM10JH?qs=g%252BEszo6zu8Mx34MmAD%2FJ0A%3D%3D
  - surface mount: https://www.mouser.de/ProductDetail/CK/PTS526-SMG15-SMTR2-LFS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
- new esp32-s3 boards by espressif

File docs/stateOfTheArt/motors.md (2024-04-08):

# Choice of the motors

"If you are a beginner we would suggest you to go with 200–400 RPM. But in general a motor with **600RPM** is fine and it’s definitely fast enough. Also, if you want to either increase or decrease the speed after buying motors, try changing the diameter of the wheels." - https://medium.com/analytics-vidhya/mm-sensors-and-motors-7fa3a870db67

## Best motors

I should have bought motors with the encoders directly built in: https://www.pololu.com/product/5211

The encoders we bought have 12CPR, but they are some disks with 20CPR that we could buy and that are compatible with our encoder: https://www.pololu.com/product/3498

## Links

- Micro Metal Gearmotors with Extended Motor Shafts (good small motors): https://www.pololu.com/category/141/micro-metal-gearmotors-with-extended-motor-shafts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
- polulu micro gearmotor 12V 650rpm (not enough power): https://www.pololu.com/product/3050
- on polulu they have the motors + encoders + wheels and they ship to switzerland!
- whole kit gearbox + wheel + encoder: https://www.robotshop.com/products/12mm-12v-micro-metal-gearmotor-w-encoder-34mm-wheel-kits-smart-robot-diy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
- good motor but very big: https://eu.robotshop.com/fr/products/12v-437rpm-3055oz-in-hd-premium-planetary-gearmotor-encoder
- 25x48mm, 6V, 14mNm (dunno what speed tho): https://eu.robotshop.com/fr/products/pololu-lp-6v-2oz-in-motor-with-48-cpr-encoder-no-gearbox
- 6V, 500rpm 12mNm (used on many uk micromice): https://thepihut.com/products/micro-metal-gearmotor-30-1
- great motor with very precise **encoder** 6V, 530rpm, 20mNm: https://thepihut.com/products/micro-metal-geared-motor-w-encoder-6v-530rpm-30-1
- small faulhaber motors (look for gearbox): https://www.faulhaber.com/de/produkte/serie/1717sr/
- online tool to configurate motors combinations faulhaber -> a good combination
  - 500rpm, 10mNm all possibilities: https://www.faulhaber.com/de/drive-calculator/fdc/show/375542/
  - 500rpm, 10mNm, 7.7V, encoders directly integrated in the motor (?): https://www.faulhaber.com/en/drive-calculator/fdc/showDetail/375542/36718-2174/

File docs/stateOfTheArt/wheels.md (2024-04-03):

# Robot wheels

We want relatively thin wheels with a rubber tires to increase the friction coefficient with the floor (the maximum acceleration of the robot is directly proportional to the friction coefficient).

We estimate that the ideal wheels dimension are around **25-30mm diameter and 10mm thick**. Smaller wheels allow for a better reactivity of the robot, but the risk is that the maximal robot speed is smaller and can be reached quickly, hence limiting the robot speed.

## 3D printing wheels

Can we 3D print the tires? If yes, what material should we use? -> paper exactly on this topic: Surface friction of rapidly prototyped wheels from 3D-printed thermoplastic elastomers

Quote: "NinjaFlex was the softest material tested, hence the one most difficult to print, and only one of the three 3D-printers used managed to produce a good quality part. This was also the material providing the highest friction coefficient for all wheel designs."

## Influence of tires on performance

- http://micromouseusa.com/?p=1111
- https://micromouseonline.com/2014/05/25/travelling-bumpy-road-micromouse/

## Ball caster wheels

- https://de.aliexpress.com/item/32844183843.html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

## Links

- https://www.jsumo.com/wheels
  - radial tightening screw
  - 33x20mm: https://www.jsumo.com/slt20p-steel-silicone-wheel-set-33mm-x-20mm-pair
  - 43x11mm: https://www.jsumo.com/jsumo-wheel-43x11mm-pair-soft-silicone
- https://www.robotshop.com/collections/robot-wheel

  - many wheels + motor options with encoder
  - not shipping to switzerland
  - https://www.robotshop.com/products/- 25d-12v-encoder-gear-motor-w-mounting-bracket-65mm-wheel-smart-robot-diy
  - already mounted gearmotor + encoder + wheel: https://www.robotshop.com/products/12mm-12v-micro-metal-gearmotor-w-encoder-34mm-wheel-kits-smart-robot-diy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

  - 43x11mm wheels that can ship to switzerland (shipping expensive): https://eu.robotshop.com/fr/products/jsumo-soft-silicone-wheel-43x11mm-pair

- 33x7mm plastic wheel: https://eu.robotshop.com/fr/products/pololu-wheel-32-7mm-black-pair
- 30x7.5mm aluminium: https://eu.robotshop.com/fr/products/30mm-aluminium-wheel

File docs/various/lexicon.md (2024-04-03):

# English - French lexicon

| English | French |
| --- | --- |
| caster wheel | roue passive avec bille |
| gear motor | moto-réducteur |
| gearbox | réducteur |
| rolling resistance | résistance au roulement |
| efficiency | rendement |
| calliper | pied à coulisse |

I2C: Leader and follower devices

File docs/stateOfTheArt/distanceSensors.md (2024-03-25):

# Distance sensors

They are 2 main technologies used in micromice:

- ToF distance sensors
- IR distance sensors

We have to choose between these two technologies.

## IR

| Pro | Cons |
| --- | --- |
| Inexpensive (0.1$) | Readings depend on orientation of surface detected and its color |
| Fast | Additional sensor conditioner required (typically resistor divider) |
| Small, does not require a lot of space | |
| Most competition micromice use IR sensors | |

Other:

- Requires an IR LED and IR photodiode, directly soldered on the board
- Using a voltage divider results in linear response depending on light intensity. We get an analog reading that still has to be processed to result in a distance measurement.

## ToF

| Pro | Cons | ≤ |
| --- | --- | --- |
| Readings consistent | Expensive (2-4$) |
| Easy I2C interface | Large separate board -> additional cables |
| No influence of surface and angle | Relatively slow (~16ms update rate) |

## Comparison of the different VL sensors

I bought the VL53L1x but looking at this comparison table, I should have taken the Vl6180X, which has smaller minimum range, smaller max range and is cheaper....

- the different sensors have the same footprint
- the only advantage of the VL53L1X would be that it has a smaller field of view (min 15°)

https://www.pololu.com/product/2490#comparison

# Links

- vl53l1x ToF sensor: https://www.tinytronics.nl/en/sensors/distance/vl53l1x-time-of-flight-tof-distance-sensor

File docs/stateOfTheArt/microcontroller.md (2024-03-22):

# Microcontroller choice

## Xiao esp32-s3

Board we wanted to use initially
Exists in Platformio
Does not have enough GPIO pins!

## ESP32-S3-DevKitC-1 (Espressif)

It appears that the regulator used on the dev board accepts maximal voltages of 2.7 to 20V. Using this board would therefore allow us not to use a voltage regulator! It would therefore be yet another component which we would not need to add to our board.

## Links

- ProS3? https://esp32s3.com/#:~:text=As%20an%20input%2C%20it%20will,4.8V%20and%205.2V.
- board with antenna on Mouser ESP32-S3-DevKitC-1: https://www.mouser.ch/ProductDetail/Espressif-Systems/ESP32-S3-DevKitC-1U-N8R8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

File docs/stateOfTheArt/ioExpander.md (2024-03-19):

# I2C to IO expander

We need an additional module that allows to have more IO pins through I2C because our microcontroller doesn't have enough pins otherwise.

Ideally we'd like to be able to do some PWM on these pins in order to put the buzzer on one of the pins, hence saving another MCU pin.

## Links

- TCA6408A (8 outputs, 1.6 to 5.5V): https://www.ti.com/product/TCA6408A#features
- XRA1200/1200P (8 outputs, 3.3V max): https://www.mouser.de/datasheet/2/146/xra1200_100_092011-1856036.pdf

- PCA9685 has 16 PWM outputs: https://www.mouser.de/ProductDetail/NXP-Semiconductors/PCA9685PW112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

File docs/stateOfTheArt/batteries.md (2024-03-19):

# Batteries of the micromouse and power management

The power supply of the micromouse is a really important aspect. We need to be able to deliver enough energy in a short time lapse in order to ensure good acceleration. We need relatively high power for the motors (with a higher voltage: 6-12V) and a low voltage for the microcontrollers and sensors (3.3V). We will therefore need a voltage regulator circuit.

- should we add a voltage meter to check the battery voltage?
- we need to be able to provide enough current! Motors require max 0.75 A each and MCU about 0.2 A -> we should be fine with a battery that can output 2A
- most micromouse use LiPo batteries

## LiPo batteries nomenclature

Imagine we have the following LiPo battery:

- 1100 mAh
- 2S1P
- 25/50C

Here is the meaning of these different parameters:

- The battery has a capacity of 1.1 Ah. This represents the amount of energy stored.
- The battery is 2S1P, which means that is is composed of 2 lipo cells in series and only 1 in parallel. We therefore have a nominal voltage twice the voltage of a single cell (3.7V), which corresponds to 7.4V.
- The last parameter quantifies the max current that can be drawn from the battery continuously and intermittently. The max continuous current is 25x the capacity (25x1.1 = 27.5A) and the max intermittent current is 50x the capacity, hence 55 A.

Battery Guide: What does the C-Rating of LiPo batteries stand for? (n.d.). Retrieved March 18, 2024, from https://www.drone-zone.de/battery-guide-what-does-the-c-rating-of-lipo-batteries-stand-for/

## The best battery so far

https://www.reichelt.de/akku-pack-li-polymer-7-4-v-1100-mah-rd-xt-1100-s2-p336956.html?&trstct=pol_8&nbc=1

- 7.4V
- length 55mm
- connector: XT60 like for drones
- max current: 27A
- weight: 55g
- capacity: 1.1Ah

What is balancing and how to deal with it?

- the battery has 2 connectors
- "Balancing plug. It's used to equalize the charge between the pack's cells when you recharge the LiPo."
- still need to find a charger

## Links

- 7.4V, 700mAh, 55g, Li-Ion battery: https://www.brack.ch/carrera-rc-rc-akku-li-ion-700-mah-7-4-v-222009
- RC-Akku Li-Ion 800 mAh 7.4V, 43g: https://www.brack.ch/amewi-rc-akku-li-ion-800-mah-7-4-v-1195382
- RC-Akku Li-Ion 600 mAh 7.4V, 45g: https://www.brack.ch/amewi-rc-akku-li-ion-600-mah-7-4-v-1195407
- USB-8.4V-1200, 9V Block, 6F22, 1200mAh Li-Ion (used in uk micromouse): https://www.accuswiss.ch/product_info.php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
- usb rechargable 9V battery: https://thepihut.com/products/400mah-li-ion-rechargeable-9v-e-block-battery

Li-Po batteries with sufficient max current:

- https://www.reichelt.de/akku-pack-li-polymer-7-4-v-1500-mah-rd-xt-1500-s2-p336957.html?&trstct=pol_6&nbc=1
- https://www.reichelt.de/akku-pack-li-polymer-7-4-v-800-mah-rd-xt-800-s2-p336954.html?&trstct=pol_10&nbc=1
- https://www.reichelt.de/akku-pack-li-polymer-7-4-v-1100-mah-rd-xt-1100-s2-p336956.html?&trstct=pol_8&nbc=1

### Battery chargers

- https://www.reichelt.de/ladegeraet-fuer-akkupacks-m6d-fuer-1-6s-max-15-a-500-w-lipo-tkrc-m6d-p364400.html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
- is this only for parallel charging? https://www.drone24hours.com/product/hglrc-tho-pro-scheda-per-bilanciamento-lipo/?lang=en
- good lipo charger for beginners with power supply included: https://oscarliang.com/isdt-608ac-lipo-charger/

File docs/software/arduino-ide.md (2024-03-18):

# Programming the ESP32-S3 through the Arduino IDE

- Tutorial: https://wiki.seeedstudio.com/xiao_esp32s3_getting_started/#software-preparation
- Board to choose: XIAO_ESP32S3

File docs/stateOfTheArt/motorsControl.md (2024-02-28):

# Control of the DC motors (motor drivers)

## Main idea

We want to create an I2C secondary that will be responsible of the control of the DC motors. It will need to have a high power circuit to power the motors and will have to process the encoders data to ensure that the desired movement is realized.

- Micro-controller: ATMega 328
- Motors driver: H bridge, e.g. L298N or LN288D (can directly control 2 motors)
- The motor speed is controlled through a PWM
- Motors must be equipped with encoders

We distinguish two different possible approaches:

1. Use a commercial speed controllers
   - in this case we would only have one main MPU that directly sends the desired speeds to the controllers
   - question: how to know the total number of impulsions from the encoders (for odometry)
     - is this info provided by the speed controller
     - do we connect the encoders directly to the leader MPU, where we count the impulsions ourselves?
     - distance sensors connected on main MPU
2. Custom speed control
   - requires the implementation of a PID regulator
   - we would have an I2C follower MPU dedicated to the control of the motors -> lots of additional code to write
   - the distance sensors are connected to the secondary MPU too

## Do we need speed controllers?

Speed controllers are used to directly control the speed of the motors, instead of controlling the current and therefore the torque. The speed controller uses the encoder data to regulate the motor speed using a closed loop system. Using a speed controller would facilitate the control of our motors on a higher level, but it adds one more circuit to the mouse, which requires power and space.

Could we not use a speed controller and instead directly control the motors from the MCU through an H bridge and use the encoder data to determine the distance that has been covered, hence realizing a position regulation instead of a speed regulation?

This approach is definitely used in some mice:

- https://www.youtube.com/watch?v=b9JztUkttgk

## Encoders

- encoders theory: https://www.posital.com/en/products/communication-interface/incremental/incremental-encoders.php
- TTL (transistor transistor logic) output encoder: encoders with two lines that have a 90° offset to be able to know the direction in which we rotate -> https://www.motioncontroltips.com/what-is-ttl/

## Links

- ready to buy motor controllers: https://eu.robotshop.com/fr/collections/motor-controllers
- I2C motor controller for 1 motor up to 2.5A speed or position controller closed loop: https://www.pololu.com/product/3142
- motors control with simple P regulator: https://ieee.berkeley.edu/micromouse-lab-5/
- micromouse online motors control: https://micromouseonline.com/2011/05/15/designing-the-motor-controller/

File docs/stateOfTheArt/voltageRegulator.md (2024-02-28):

# Voltage regulator

We want to convert the voltage of the battery to 3.3V in order to power the micro-controller and the sensors.

## ADP7102ARDZ-R7

- max 300mA output -> is it enough?

## Links

- variable voltage regulator max 20V to 3.3V: https://www.mouser.ch/ProductDetail/Analog-Devices/ADP7102ARDZ-R7?qs=WIvQP4zGanhyecxhoOTYew%3D%3D

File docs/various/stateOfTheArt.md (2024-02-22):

# State of the art

## Green giant

- 2012-2013 micromouse with faulhaber motors: https://www.faulhaber.com/de/produkte/serie/1717sr/
- vmax = 4.5 m/s, search: 2m/s
- acc max: 13.5m/s^2
- IR sensors
- double pair of wheels for bigger accelerations

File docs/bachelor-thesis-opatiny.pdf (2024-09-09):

## Algernon: Design of a Micromouse Robot With a Remote Debug Interface

## Bachelor Thesis in Micro-Engineering

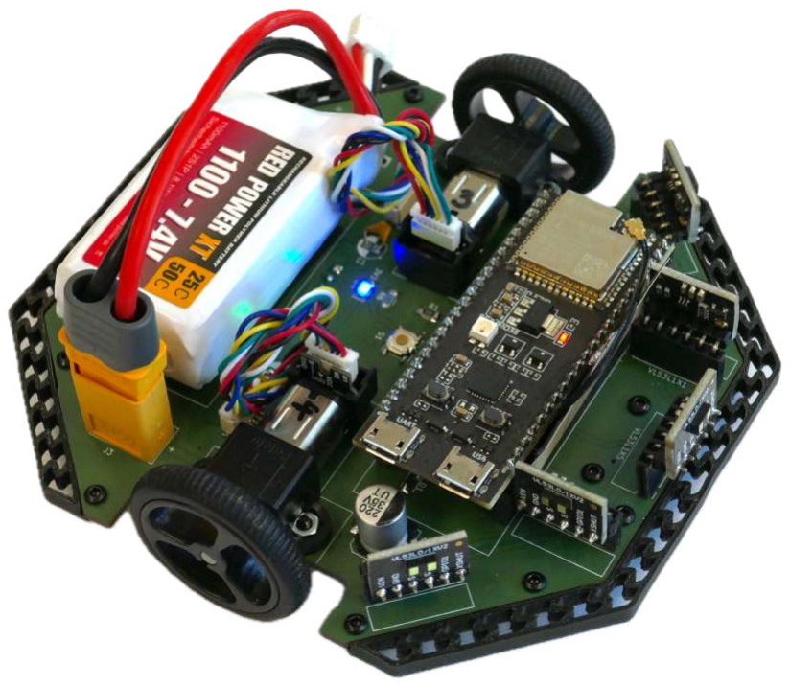
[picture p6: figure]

Regensburg, August 19, 2024 | Océane Patiny
| Supervisors Prof. Dr. Martin Weiss (OTH)

## M. Yves Chevallier (HEIG-VD)

## Erklärung zur Bachelorarbeit

1. Mir ist bekannt, dass dieses Exemplar der Bachelorarbeit als Prüfungsleistung in das Eigentum der Ostbayerischen Technischen Hochschule Regensburg übergeht.
2. Ich erkläre hiermit, dass ich diese Bachelorarbeit selbständig verfasst, noch nicht anderweitig für Prüfungszwecke vorgelegt, keine anderen als die angegebenen Quellen und Hilfsmittel benutzt sowie wörtliche und sinngemäße Zitate als solche gekennzeichnet habe.

Regensburg, den 10. August 2024

## Grammar and syntax

The grammar and syntax of this report were improved using the free version of the Elphas (https://elephas.app/) software v. 9.35. The chat model used is OpenAI’s gpt-4.

Abstract

In this report, the comprehensive steps necessary for the design, assembly, and testing of a custom autonomous robot are detailed. The project drew inspiration from micromouse competitions, where small, autonomous, maze-solving robots compete to solve an unknown maze in the least amount of time. The primary focus of this project was the design of a micromouse from the ground up. This encompassed both electrical and mechanical design, along with the creation of a custom PCB. A physical prototype of the robot was successfully assembled and tested.
The robot is equipped with five Time-of-Flight (ToF) distance sensors, an accelerometer, and two brushed DC motors with magnetic encoders. The microcontroller utilized is an ESP32-S3, and a 2P1S LiPo battery serves as the power supply. On the software front, each sensor was independently tested and found to be functional. A rudimentary odometry task was implemented, allowing for the tracking of the robot’s position. Speed regulation of the wheels was also incorporated. The maximal speed the robot can reach 1.05 m/s, and its maximal acceleration is 1.5 m/s

2
. Finally, a remote debug interface utilizing WiFi was developed to enable real-time visualization of the robot’s status.

## Acknowledgements

First and foremost, I would like to express my gratitude to Prof. Martin Weiss, who kindly agreed to be my supervisor at Ostbayerische Technische Hochschule (OTH) in Regensburg, Germany, despite never having met me before. I wish to thank him for his warm welcome to this school, which was brand new to me as an exchange student. I could not have brought this project to fruition without Prof. Weiss’s Swiss counterpart, Mr. Yves Chevallier, who kindly agreed to be my supervisor at the School of Business and Engineering Vaud (the HEIG-VD), my home university.

I am also deeply grateful to all the professors of the HEIG-VD who made themselves available to answer my technical questions in their respective areas of expertise: Mr. Michel Etique, Mr. Michel Girardin, and Mr. Mikaël Krummen. Another person whom I would like to thank for always lending an attentive ear to my various struggles is my dad, who never seems to get bored of my robotic shenanigans. In addition, I would like to extend my sincere thanks to my friend Bo, who considered redoing some of my figures as an entertaining graphic design exercise.

Finally, special mention goes to all of my friends, old and new, who showed interest in my project, continuously asked for updates about my little robot, and never failed to encourage me when I felt like I would never manage to finish this project. Working on such an ambitious project in an unknown environment, without most of the tools I am accustomed to, indeed felt like jumping off a cliff... without a parachute.

# Contents

Acknowledgements

1 Introduction | 13
2 State of the Art | 17
3 Solutions | 41
4 Theory | 47

CONTENTS

5 Electronics | 73
6 PCB Design | 81
7 Mechanical Design | 87
8 A Custom Maze Design | 91
9 Software | 97

CONTENTS

9.12 WiFi Debug Interface | 105
10 Results | 109
10.1 Hardware | 109
10.2 Software | 110
10.3 Maximal Speed and Acceleration | 111
10.4 Price | 112
10.5 Autonomy | 112
10.6 Review of the Project Planning | 113
10.7 Improvements | 114
10.8 Perspectives | 114
11 Conclusions | 115
Bibliography | 121
Appendix | 123
1 | Experiment: Maximal Speed and Acceleration | 123
2 | Experiment: Measurement of wheels speed | 124
3 | Experiment: Motor’s speed vs voltage | 125
4 | PCB schematics and project planning | 128

# Chapter 1

# Introduction

They called the mouse Algernon. Algernon was in a box with a lot of twists and turns like all-kinds of walls and they gave me a pencil and a paper with lines and lots of boxes. On one side it said START and on the other end it said FINISH.

Flowers for Algernon
- Daniel Keyes

The Amazing MicroMouse contest is a robotics contest first launched in the IEEE Spectrum magazine in 1977. The principle of the contest can be explained very easily: you have to create an autonomous robot (a mouse) that must solve an unknown maze as quickly as possible [1].
Since the first edition, the contests have continually gained more attention, spreading worldwide. By 2014, there were already around 100 contests held that year, and their popularity is always increasing [1]. Throughout the years, hundreds of micromice have been built, featuring a vast range of inventive solutions to various challenges. Research is also conducted in the field, often leading to scientific publications.
Whether university students, makers, or graduated engineers, anyone can have fun working on a micromouse project. Depending on the individual’s skills, it is possible to buy a ready-to-program kit, or alternatively, fully build the micromouse from scratch. It is, therefore, an extremely versatile project idea, allowing people with more or less previous knowledge to engage with robotics in a fun way [69]. Indeed, there is something very satisfying about making a small robot that can navigate by itself. It is for these various reasons that I decided to tackle it myself, using my bachelor thesis as a perfect opportunity to dive deep into the micromouse world. The Amazing MicroMouse contest, a robotics competition, was initially introduced in the IEEE Spectrum magazine in 1977. The premise of the contest is straightforward: participants are required to construct an autonomous robot (termed a mouse) that can navigate an unfamiliar maze in the shortest time possible [1].

13

14 | CHAPTER 1. INTRODUCTION

Figure 1.1: Some of micromice that participated in the very first contest (1977-1979) [30]

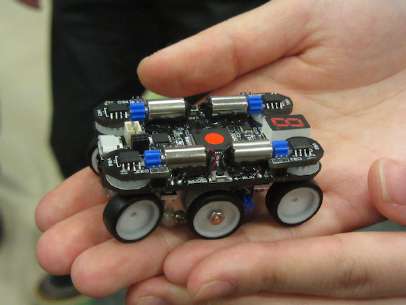
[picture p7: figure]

Figure 1.2: A mouse from the All Japan Half-Size micromouse contest 2017 [34]

## 1.1 Outline of the Contests Rules

The exact rules for micromouse contests vary slightly from one contest to another, but the principle remains the same. The robot must be fully autonomous and should therefore not communicate with the outside. The maze layout is kept secret until the beginning of the competition. It is therefore not possible to program the maze beforehand. The maze is composed of 16x16 square cells with 18 cm sides. The walls are 12 mm thick and 50 mm high. The start of the maze is always in one of the corners, and the goal is a 2x2 cells space in the center of the maze. Figure 1.3 shows a typical maze layout. Each team has 10 min of access to the maze and the fastest run from start to finish during this time is registered [51].

Figure 1.3: Example of a full-size micromouse maze [15]

1.2. MOTIVATIONS | 15

## 1.2 Motivations

For me, the discovery of the amazing micromouse contests happened through Veritasium’s excellent video "The Fastest Maze-Solving Competition On Earth," released on 24.05.2023 on YouTube [29]. Like all of Derek Muller’s videos, the content is well-researched, interesting, and entertaining, and it immediately intrigued me. Conveniently, I was searching for a thesis subject at the same time, and it became obvious to me that I wanted to work on the design of my own micromouse.
Micromice are interdisciplinary projects that encompass all fields of micro-engineering: electronics, mechanics, programming, and robotics. For this reason, it appears as the perfect project for my thesis, even though it is very ambitious. To me, the bachelor thesis is an opportunity to experiment and step out of my comfort zone, even if I risk not achieving all I want to do. Indeed, it is probably one of the last situations where we can "fail" without it mattering too much.

## 1.3 Objectives

The goal of this project is to design a micromouse from scratch in 6 months. To frame the project a little bit more, the goal is to get as close as possible to having a robot that can solve a standard micromouse maze autonomously. It is likely that this objective is too ambitious considering the time available, however, it can serve as a clear guideline throughout the project. Since the time span we have to realize a project of this complexity is relatively limited, we will focus on the electronic and mechanical design, as well as the communication with the different sensors and the control of the robot movements. The main aspects of the project will hence be the following:

– State of the art: See what already exists, what technologies are commonly used, and what the well-established standards are.

– Choice of the components: List the different electronics needed and find the commercially available components.

– PCB design and assembly: Firstly, realize the PCB schematic with all the required components and then create the layout of the PCB. Order the custom PCB, assemble it, and test it.

– Retrieve sensors data: The micromouse will integrate a variety of sensors. We must be able to communicate with all of them and retrieve the data.

– Control of the motors: Be able to control the motors to move at a desired speed. This step will require the implementation of PID regulators. We will also need to implement an odometry algorithm, which allows us to know the robot’s position, orientation, and speed.

– Wall following: The robot should be able to navigate in a corridor without bumping into walls. This implies a regulator on the robot’s position in the corridor.

Additionally, we will try to develop good debugging tools as we go. Indeed, being able to easily see the current state of the robot, the different commands that are processed, and the sensor data will allow us to better understand the robot’s behavior and therefore find potential bugs.

16 | | | CHAPTER 1. INTRODUCTION

## 1.4 Planning

The bachelor thesis is a 450 h work project led during the last semester of the bachelor studies. This project was realized during an exchange semester at the Ostbayerische Technische Hochschule, in Regensburg, Germany. It officially started on the 18th of March and ended on the 18th of August 2024 (even though in practice we started one month earlier). In order to ensure the feasibility of the project, all of the tasks to be realized were listed and a plan spreading them over the duration of the project was created. In this process, ambitious decisions were made (short deadlines, little time for errors), while still trying to make honest estimations of the time each step would take. The resulting plan can be found in the annexes at the end of this document (see Figures 11.6, 11.7 and 11.8). The core milestones are, however, summarized in Table 1.1.

Dates | Nb. weeks | Type | Focus
19.02 - 17.03 | 4 | Doc. | State of the art, documentation and architec-
| | | ture choice, custom maze design and manu-
| | | facturing
18.03 - 12.05 | 8 | Hardware | Electronic design, PCB design and manufac-
| | | turing, assembly of robot v1
13.05 - 02.06 | 3 | Hardware | Bug fixes in the hardware, final robot hard-
| | | ware done
03.06 - 30.06 | 4 | Software | Test of all the sensors and programming of
| | | motor control task, driving straight in a cor-
| | | ridor, create WiFi debug system
01.07-04.08 | 5 | Software | Turning, following a predefined path in
| | | maze, implement floodfill algorithm
05.08-18.08 | 2 | Doc. | Report

Table 1.1: Summary of the project planning (Doc. stands for documentation).

## 1.5 Documentation and Project Files

Throughout this project, GitHub has been used as a project management tool, as well as a version control tool. All of the data related to this project can be found in the three following repositories:

– Hardware related files, documentation and MatLab scripts: https://github.com/opatiny/micromouse
(commit a043f868b5adddb9797485b194d83862c804f196)

– C++ software for the micromouse: https://github.com/opatiny/ms-software
(commit d6f4fc6eaca07a7fbeb5fb862d9489f111c2e57a)

– TypeScript code for the debug web page: https://github.com/opatiny/ms-webpage
(commit becbb41689782ab37acf18b62f3899d26b75d5da)

All of our work is open-source: the hardware repository is under CERN-OHL-P-2.0, whereas the software is under MIT.

# Chapter 2

# State of the Art

To be as exhaustive as possible in this state of the art, 10 different micromouse projects have been analysed. This allowed us to see the solutions used for the different parts of the robot, as well as establish which technologies are the most widespread. The list of projects studied, their characteristics, as well as links to the web pages where the information has been found can be accessed using the link in the footnote.²

## 2.1 Price

As the idea for this project was a personal proposition, there are no fixed requirements on any aspect of it. We do, however, need to define an approximate price target for the robot, since that will limit the technologies we can use for the different components. In order to set a price range, various existing mobile robotics and micromouse kits were analyzed. Table 2.1 summarizes some of these projects, as well as their respective prices. Based on this table, we could deduce that a reasonable price for our micromouse would be around €150, similar to the Project Futura robot. Indeed, in terms of features, it is the robot that is most similar to what we would like to realize in this project.

Name | Description | Price [€]
Thymio II | Open-source educational differential drive mobile robot developed in Switzerland | 250
PICAXE ’PICone’ Micromouse | Self-assembly micromouse kit | 125
Micromouse T01 Kit | Self-assembly micromouse kit based on the UKMARSBOT platform | 75
Project Futura | Pre-made high-performance low-cost Mouse kit used as a teaching tool | 150

Table 2.1: Breakdown of the robot’s price, excluding all shipping costs.

2You can find the recapitulative state of the art here: https://tinyurl.com/ms6mrj4p

17

18 | CHAPTER 2. STATE OF THE ART

## 2.2 Types of Motors

The following sections describe some of the motor technologies that are used in existing micromouse robots. Their characteristics are outlined, and their advantages and drawbacks are summarized.

### 2.2.1 Brushed DC Motors

Brushed DC motors (BDC motors) are some of the most widespread motors used in robotics applications because of their low price and how easily they can be controlled [33]. Indeed, simply applying a DC voltage to the motor’s terminals allows it to spin. Moreover, since the motors use direct current, they are particularly suitable for battery-powered devices.

The speed of a DC motor is directly proportional to the effective voltage applied to it. A pulse width modulation (PWM) signal can therefore be applied to the motor in order to control its speed [57]. Since the power required for the motors cannot be directly output by the microcontroller, a full-bridge motor driver has to be used. This component allows the low-power circuit of the microcontroller to be linked with the high-power circuit of the battery.

A disadvantage of these motors, however, is that there is no way to know at what speed the motor is actually spinning without using additional sensors. For this reason, encoders are added to the motor’s shaft. The encoders allow the rotation of the shaft to be measured. The existing types of encoders are discussed in Section 2.4.
Based on the projects that we studied, we can see that BDC motors are the most widespread in micromouse projects (they are used in 7 out of 10 projects).

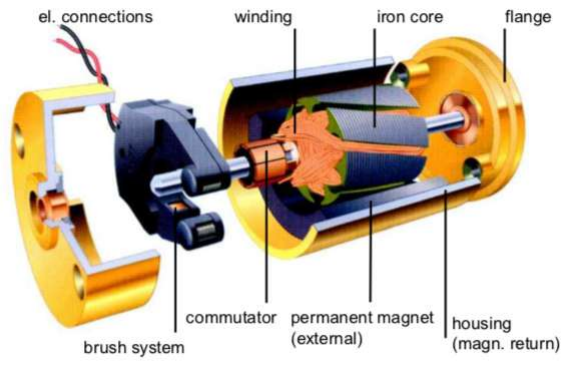
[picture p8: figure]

Figure 2.1: Schematic of a brushed DC motor [9]

2.2. TYPES OF MOTORS | 19
Advantages | Drawbacks
High power to weight ratio | Absolute position unknown, requiring
| encoders to monitor motor movement
Mechanical commutation (no electronic controller needed) | Motor brushes tend to wear down, lim-
| iting motor lifetime
Often found pre-assembled with a gear- box | Adding a gearbox to a motor increases
| angular play
Wide variety of models varying in size,
torque, speed, etc.

Table 2.2: Advantages and disadvantages of brushed DC motors.

### 2.2.2 Coreless DC Motors

Coreless DC motors closely resemble standard BDC motors, with the exception that the rotor is self-supporting and not wound around an iron core. This is illustrated in Figure 2.2. The absence of an iron core significantly reduces the rotor’s weight and its inertia, thus improving the motor’s dynamics.

Figure 2.2: Schematic of a coreless DC motor [26]

Advantages | Drawbacks
Large torque to weight ratio compared to other BDC motors | Uses brushes, which limit the motor’s lifespan
Can be controlled using PWM like other BDC motors | Requires encoders

Smaller than conventional DC motors

Table 2.3: Advantages and disadvantages of coreless DC motors.

20 | CHAPTER 2. STATE OF THE ART

### 2.2.3 Stepper Motors

Stepper motors are constructed with pairs of coils on the stator and a toothed, magnetised rotor, as illustrated in Figure 2.3. By activating the pairs of coils in sequence, the teeth of the rotor align with the coils, resulting in a movement of one step. Typical stepper motors have 200 incremental steps per full rotation, implying that each step is 1.8

| ◦
[36]. Therefore, unlike brushed DC motors, the movement of a stepper motor is not continuous but discrete. The motor is controlled using electrical pulses, the frequency of which determines the motor’s speed [49]. The control is open-loop, meaning there is no need for encoders. However, if the motor misses steps, which can occur if the torque is too large, there is no way to determine the motor’s absolute position anymore.

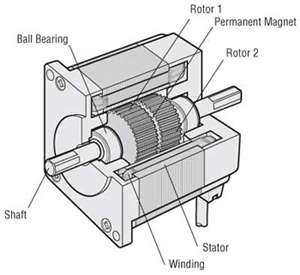
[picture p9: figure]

Figure 2.3: Schematic of a stepper motor [14]

Advantages | Drawbacks
No accumulation of error on the motors’ position as long as no steps are missed | Full-step control of the stepper limits the minimal angular displacement to 1 step (typically 1.8 ◦ )
No need for encoders | No feedback to indicate missed steps
Overload safe: the motor can’t be dam- aged by applying high torque | Prone to vibration and noise
No brushes, which are prone to wear | High power consumption even when the motor is not moving

Table 2.4: Advantages and disadvantages of stepper motors. This table is largely based on [37].

2.3. CONFIGURATION OF THE MOTORS AND WHEELS | 21

## 2.3 Configuration of the Motors and Wheels

All ten projects that we have studied are based on a differential drive. Differential wheeled robots are equipped with two wheels, each connected to their own motor. The wheels are controlled separately. The combination of the motors’ speeds can result in forward motion, turning, and backward motion of the robot, as illustrated in Figure 2.4. According to our research, most competition-winning micromice use a variation of a differential drive [53]. However, we will discuss one interesting project using a belt-based drive in Section 2.3.4.

Figure 2.4: Differential drive robot principle: The combined speeds of the wheels allow the robot to drive straight, turn, and rotate on the spot [23]

Despite the drive principle being relatively similar among most of the micromice, there is still a wide variety of motor configurations, which will be detailed in the following sections.

22 | CHAPTER 2. STATE OF THE ART

### 2.3.1 Wheels Directly on Motors’ Shafts

The simplest way to mount the wheels is to connect them directly to the motors’ shafts. This approach is most commonly used in beginner micromouse projects, as well as in some of the open-source kits that can be found online, such as ukmarsbot by the UK Micromouse and Robotics Society (see Figure 2.5). In the case of this robot, the motors are equipped with a D-shaped output shaft. By using a wheel with a D-shaped bore, the wheel can be mounted without any screws, simply by using the friction between the shaft and the bore (this is also visible in Figure 2.5).

Advantages | Drawbacks
No additional transmission means fewer parts that can break | Motors’ length limited to half of the robot’s width

Since no transmission is used, there is
more space on the PCB for other components

Table 2.5: Advantages and disadvantages of wheels directly on the motors’ shafts.

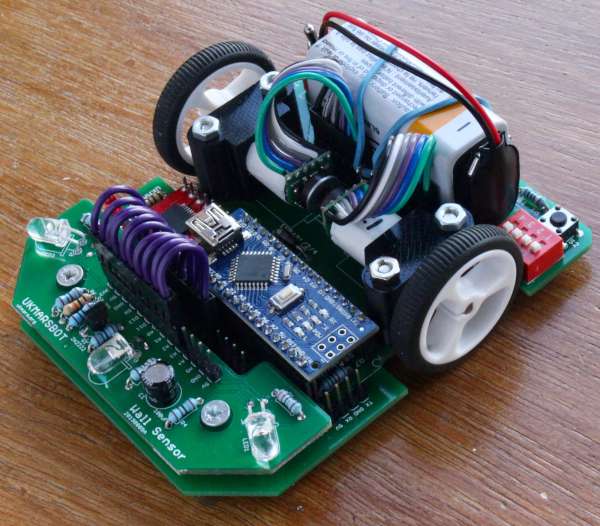
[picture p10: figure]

Figure 2.5: Ukmarsbot’s wheels are directly attached to the motors’ shafts. [25]

2.3. CONFIGURATION OF THE MOTORS AND WHEELS | 23

### 2.3.2 Wheels on Axes Parallel to Motors’ Shaft

Instead of being directly on the motors’ shaft, the wheels can be mounted on a parallel axis. There are two possibilities: either the two motors are mounted on the same side of the wheels, like in Figure 2.6, or they are placed on the opposite side of the wheels. The second possibility allows for longer motors, spanning almost the entire width of the robot. The motors can thus be more powerful, resulting in better performance of the final robot. Since the motors are no longer coaxial with the wheels, a transmission must be used to transfer the torque to the wheels. The transmission would typically use spur gears or belts. This design also has another advantage, which is that a reduction can be added at the level of the transmission, allowing optimization of the wheels’ speed and torque for the micromouse.

Advantages | Drawbacks
Less restriction on motors’ length | Additional mechanical play if gears are
used
Possible additional reduction with gears
or belt

Requires the design of more mechanical components
Takes up more space on the PCB

Table 2.6: Advantages and drawbacks of wheels on axes parallel to the motors

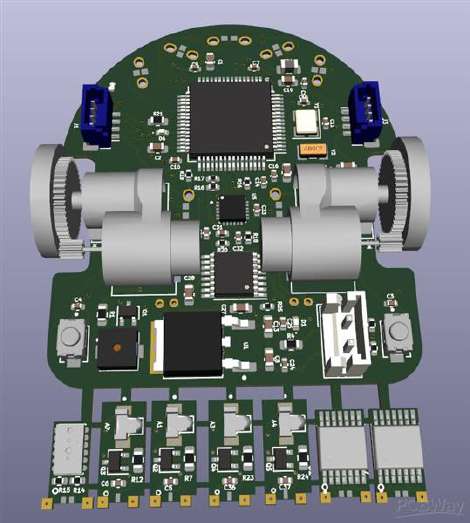
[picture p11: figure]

Figure 2.6: Mushak, by Chimnay Lonkar, uses wheels on axes parallel to the motors’ shafts. [16]

24 | CHAPTER 2. STATE OF THE ART

### 2.3.3 Wheels Perpendicular to Motors’ Shaft

Another interesting approach is to have the motors perpendicular to the wheels’ axes. There are two different variants: the motors can either be placed vertically (see Figure 2.8), or along the longitudinal axis of the mouse (as shown in Figure 2.7). In both cases, a right-angle transmission is required (typically conical gears). This approach is interesting because it allows for the use of longer motors. In the case of the vertical motors, it also leads to a smaller footprint of the motors on the PCB, leaving more space for other components.

Advantages | Drawbacks
Less restriction on motors’ length | Conical gears required (additional me-
| chanical play)
Possible additional reduction at the level of the conical gears | The wheels can’t be placed in the middle
| of the robot

Table 2.7: Advantages and drawbacks of longitudinal motors

Figure 2.7: Jim Remington’s micromouse has motors along the longitudinal axis of the robot and uses conical gears for the transmission of the torque to the wheels. [22]

Advantages | Drawbacks
Motors take less space on the PCB | Conical gears required (additional me-
| chanical play)
No physical limitation on motors’ length | The motors being vertical raise the
| robot’s center of mass
Possible additional reduction at the level
of the gears

Table 2.8: Advantages and drawbacks of vertical motors

2.3. CONFIGURATION OF THE MOTORS AND WHEELS | 25

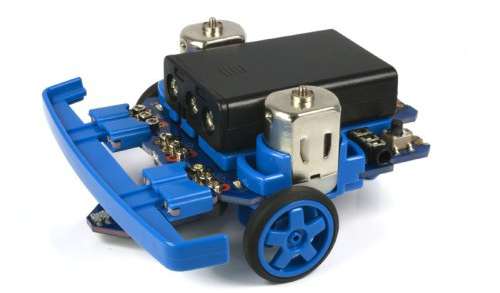
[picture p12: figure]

Figure 2.8: The Picaxe Microbot kit uses vertical motors and conical gears to transmit the movement to the wheels [10]

### 2.3.4 Belt Based Systems

Instead of using gears as in all the previous mice, it is also possible to use belts for transmission. Belts have multiple advantages:
– They are very lightweight.

– They allow for the addition of a reduction in the same way as with gears.

– The motor’s shaft and the wheel axis can be further apart than with spur gears.

– Thanks to the tension in the belt, there is little additional mechanical play.
These systems, however, require an additional tensioning mechanism, which can make them more complex to design. The Shi On micromouse project (see Figure 2.9) is one of the few that actually implements belts in their design. In the case of this mouse, three pairs of wheels are used, and the front and back ones are oriented by a vertical motor through a belt transmission. This is one of the rare projects not using a differential drive approach. Instead, the robot has "drive motors", responsible for acceleration, and "steering motors", used to make the robot turn [18].

Figure 2.9: The Shi On micromouse uses 3 pairs of wheels. The motors are vertical and the motion is transmitted using belts that actuate the front and the back wheels. [18]

26 | CHAPTER 2. STATE OF THE ART

## 2.4 Encoders

Rotary encoders are necessary to measure the displacement of the DC motors. Knowing the movement of each wheel is essential to determine the robot’s speed and orientation. Two main types of encoders used: magnetic and optic. More recently, capacitive encoders have also been developed, but they are not as widespread. Encoders generally output a digital signal with a certain number of pulses per full rotation of the motor. This is referred to as the "counts per revolution" (CPR). The higher the CPR, the better the resolution of the encoder.

### 2.4.1 Magnetic Encoders

Magnetic encoders are based on Hall effect sensors. They consist of a rotary magnetic disk with alternating south and north poles, and a magnetic sensor. When the disk rotates, the sensor detects variations in the magnetic field and outputs a digital signal with the transitions from positive to negative magnetic field. Counting the number of transitions allows to determine the rotary displacement of the motor. Some magnetic encoders, like the RM08 Miniature Rotary Magnetic Encoder [61], can also output a sinusoidal signal, which would need to be processed to deduce the rotary displacement.

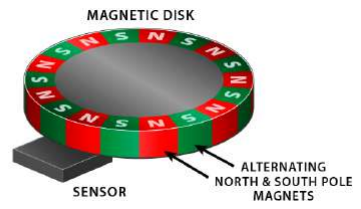
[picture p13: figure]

Figure 2.10: Principle schematic of a magnetic encoder [11]

### 2.4.2 Optical Encoders

Optical encoders are based on light instead of magnetic fields. In this case, the rotating disk is perforated with thin radial slits. As the light passes through the slits, it is detected on the other side by a light sensor, thus allowing to determine the incremental displacement. Unlike magnetic encoders, optical encoders are sensitive to ambient light and contamination (dust, oil) than magnetic encoders [11].

Figure 2.11: Principle schematic of an optical encoder [11]

2.5. DISTANCE SENSOR TECHNOLOGIES | 27

## 2.5 Distance Sensor Technologies

For an autonomous robot, sensing its environment is crucial to deduce its location and eventually build a map of its surroundings. Of course, not all autonomous mobile robots (AMRs) have the same requirements. Depending on the application, different technologies should be used, each providing varying degrees of information about the robot’s environment. If we venture beyond the scope of micromice, where the maze is a relatively standardized environment that is easy to navigate, the task of simultaneous localization and mapping (SLAM) becomes significantly more challenging. Robots need to process vast amounts of data and extract useful information from it. SLAM is a well-known challenge in mobile robotics, as presented by Thrun et al. in their book Probabilistic Robotics.

"In SLAM, the robot acquires a map of its environment while simultaneously localizing itself relative to this map. SLAM is significantly more difficult than
all robotics problems discussed thus far: It is more difficult than localization in that the map is unknown and has to be estimated along the way. It is more difficult than mapping with known poses, since the poses are unknown and have to be estimated along the way." [8]

The typical sensors used on these more generic robots are the following [4]:

– 2D or 3D LiDAR (Light Detection and Ranging)

– Camera

– Stereo camera: uses left and right images to get an idea of the distance

– Infrared sensor

– Ultrasound sensor

In the case of micromice, we must consider that the microcontroller is relatively computationally limited, and therefore sensors generating a lot of data to process are not ideal. This is why the vast majority of micromouse projects use some sort of distance sensors. These generally fall into one of three categories: ultrasound sensors, infrared sensors, or time of flight sensors.

### 2.5.1 Ultrasound Sensors

Ultrasound sensors consist of an emitter (transducer) that generates ultrasonic waves (over 20 kHz), and a sensor, which acts as a microphone. The device emits short bursts of sound and measures the time required for the sensor to detect the reflected wave. Since the duration, as well as the speed of sound, are known, the distance to the obstacle can be calculated [50]. The output signal of the sensor is typically an analog voltage that is directly proportional to the distance to the object. It is therefore easy to use with a microcontroller. Ultrasonic sensors are an interesting technology because they are independent of ambient light, presence of dirt, target color, and material (generally). However, they can be affected by soft material which would absorb the sonic wave. These sensors would not be ideal when used with targets that are not perpendicular to the sound wave, as it would not bounce back towards the receiver. In addition, if many sensors are

28 | CHAPTER 2. STATE OF THE ART

used, there can be crosstalk issues, which means that the signal of one sensor will be detected by another one, leading to aberrant readings [50]. In the case of micromice, these sensors are rarely used due to their bulky size. Out of the ten projects on our list, only one used ultrasound sensors.

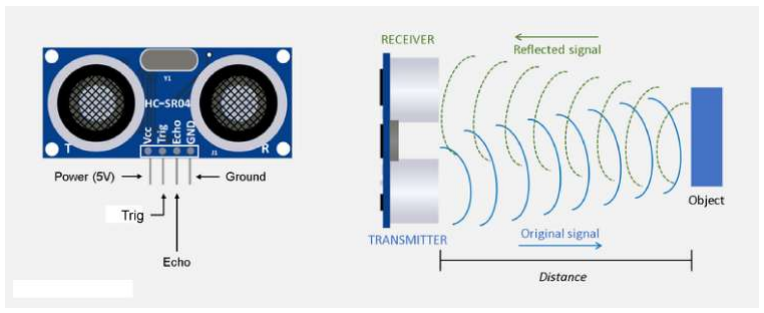
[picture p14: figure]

Figure 2.12: Schematic of an ultrasonic sensor [17]

Advantages | Drawbacks
Unaffected by dust, color, target material

Target orientation can impact readings

Relatively inexpensive (around 4 euros) | Dimensions: | Typical board size is
| 45x20x15 mm
Longer range than infrared sensors (up
to 4 m)

Possible crosstalk issues when multiple sensors are used

Table 2.9: Advantages and disadvantages of ultrasound sensors.

### 2.5.2 Infrared Sensors

Infrared distance sensors consist of an infrared (IR) LED and a photo-transistor that acts as a light detector. Similar to ultrasound sensors, the reflected light is measured. The intensity of the light returned by the sensors holds the information about the distance to the target. These sensors can be custom-built from an IR LED and a photo-transistor. They are also compact and inexpensive: both the LED and the photo-transistor cost a few tens of cents. A voltage divider allows the reading of the analog voltage returned by the sensor and deduces the intensity of the reflected light and therefore the distance. However, this technology has several issues. For instance, it is very sensitive to ambient light, dust, and the color of the target, all of which will impact the amount of light returning to the receiver. Camera auto-focus systems, which are also infrared, can interfere with the sensors. Furthermore, the orientation of the target is critical, as the amount of reflected light varies greatly with the angle of the surface [43].

Infrared distance sensors are the most widely used in micromouse projects (8 out of 10).

2.5. DISTANCE SENSOR TECHNOLOGIES | 29

Figure 2.13: Principle of an infrared distance sensor [12]

Figure 2.14: Typical electrical circuit of an IR sensor [12]

Advantages | Drawbacks
No additional PCBs required: the LED and photoresistor can be bent at 90◦ | Target orientation impacts readings
Inexpensive (around 20 cents for emitter + receiver) | Sensitive to ambient light, dust, target
| color
Fast readings | Possible crosstalk issues with multiple
| sensors

Table 2.10: Advantages and disadvantages of infrared sensors.

### 2.5.3 Time of Flight Sensors

Time of Flight (ToF) sensors is a term used for IR distance sensors. Instead of measuring the amount of light reflected, the time for the light to go from the emitter to the receiver is measured. There are two main ToF sensor technologies. The first variant emits light with modulated intensity, and the intensity of the reflected light is measured. By measuring the phase difference between the emitted and detected signals, the distance to the target can be deduced. These sensors are called indirect ToF. The second type of sensors is called direct ToF sensors. In this case, the time for the emitted light to bounce back to the receiver is measured [31]. The fact that this technology works for distances of only a few centimeters is really impressive, since a round trip for a 1 cm distance would only be 67 ps [63]. The distance d is then simply derived from the following formula, where c is the speed of light and ∆t the time for the light to bounce back:

d =

| ∆t · c
| 2 (2.1)

Time of flight sensors can directly output the measured distance. Many ToF sensors can be interfaced using the I²C protocol [63], which is supported by most microcontrollers.

30 | CHAPTER 2. STATE OF THE ART

There are two possibilities: either only buy the distance sensor chip, or buy a shield integrating it. The issue is that the component itself is a very compact SMD package and can only be soldered with an oven (difficult to do without appropriate materials). Moreover, the sensors have to point perpendicularly to the robot’s main PCB, which cannot be achieved with the SMD chips. Buying a fully integrated board allows the sensors to be added to the robot using standard pin headers. One issue, however, is finding ToF with the smallest possible PCB, since the space on the robot is limited.

This type of sensor is used in some beginner and intermediate micromouse projects, whereas competition-winning projects prefer infrared sensors. Of all the projects we analyzed, only 1/10 used ToF sensors.

Figure 2.15: The VL53L1X time of flight distance sensing board by Adafruit (board around 25x20 mm) [19]

Advantages | Drawbacks
Fully integrated device with I²C commu- nication | Expensive compared to IR and ultra- sound alternatives (around €10)
Readings are independent of the surface orientation | I 2C communication is slower than a sim-
| ple ADC with an infrared detector. Can
| limit the robot’s reactivity.
Range from 30 to 4000 mm | Depending on the model, the devices
| have a minimum range of a few centime-
| ters!
Relatively small (compared to ultrasound)

Table 2.11: Advantages and disadvantages of ToF sensors.

2.6. INERTIAL MEASUREMENT UNIT (IMU) | 31

## 2.6 Inertial Measurement Unit (IMU)

Inertial measurement units are devices that are designed to measure an objects motion. They typically integrate an array of different sensors, which allow to measure the acceleration, rotation and velocity [52]. IMUs are often integrated in mobile robots as a relative positioning technology, which means that the current position depends on the previous ones. Indeed, the position and orientation of the robot can actually be deduced from the IMUs data by integrating it. Double integration of the acceleration results in the robot’s position, whereas integrating the angular rate yields to the angle of the robot. This positioning method is known as Inertial Navigation System (INS) [3]. One issue with this positioning method, however, is that the errors accumulate over time, meaning that the accuracy of the position gets worse as the robot moves. On the other hand, it has multiple advantages:

– The IMU can sense movements in three dimensions, unlike odometry, which requires a contact with the floor at all times.

– IMUs are compact sensors, which do not require external connection for the positioning (on the contrary of GPS, for instance). This allows to use them indoors.

– Unlike odometry, the IMU is not impacted by the wheels slipping on the floor.

Adding an IMU to a micromouse hence provides useful data on the robot’s state. Especially, it allows to detect when the wheels are slipping, and correct the estimated position accordingly. Out of the 10 project that we studied, 5 used an accelerometer.

32 | CHAPTER 2. STATE OF THE ART

## 2.7 Batteries

Since the robot must be autonomous, it requires its own energy source, in this case, batteries. Below is a summary of the most significant characteristics of a battery:

– Capacity: The amount of stored energy

| – Nominal voltage: The voltage of the battery when charged
| – Maximum continuous discharge current: The maximum continuous current that
the battery can provide
| – Maximum intermittent discharge current: The maximum current that can be drawn
from the battery for a brief period

Choosing the most suitable battery technology can be challenging, regardless of the application. This is why the paper Energy Sources of Mobile Robot Power Systems: A Systematic Review and Comparison of Efficiency by Mikolajczyk is particularly intriguing, as it offers quantitative data about different battery chemistries, as well as a guide to selecting the appropriate battery chemistry [5]. Figures 2.12 and 2.16 display some of the most relevant images from the paper.
In the case of micromice, the weight-to-capacity ratio must be as small as possible. Indeed, a lower overall mass will allow greater acceleration of the robot. According to 2.16, the most optimal chemistry is therefore lithium polymer. From the projects we studied, 9 out of 10 used LiPo batteries. The final project used a nickel-metal-hydride (NiMH) battery.

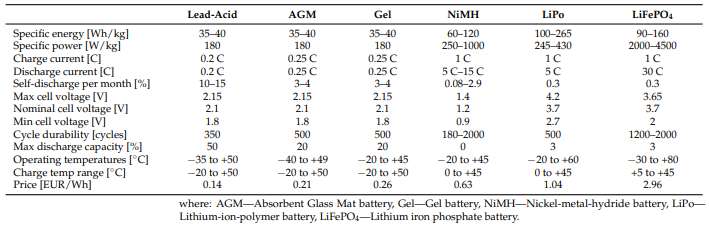
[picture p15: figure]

Table 2.12: Battery properties depending on the chemistry [5]

2.7. BATTERIES | 33

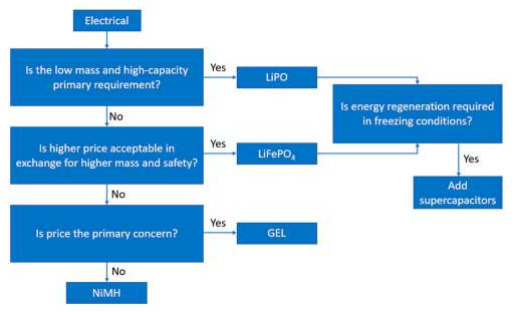
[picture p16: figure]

Figure 2.16: Procedure to choose the most suitable battery chemistry [5]

34 | CHAPTER 2. STATE OF THE ART

## 2.8 Microcontroller

The choice of the microcontroller unit (MCU) for the micromouse will impact the programming language used for the project, its ease of debugging, and the computational power of the mouse. The selection of the MCU involves a trade-off between several criteria, such as memory, power, number and type of pins, and the ability to connect to the internet. For micromice, there are additional constraints to consider:

| – The device is battery-powered, so it’s essential to minimize overall power consump-
tion.
| – The robot incorporates numerous sensors, the data from which must be processed
simultaneously.
| – The robot must be capable of processing real-time data to ensure accurate position
control.
| – The robots must make decisions quickly, as the best run times for full-size micromice are currently around 8 seconds (winner of the all Japan classic micromouse contest

2017) [54].

| – The MCU requires sufficient interrupt pins to allow quadrature encoding.
| – The device needs enough memory to store the map of the maze (at least 1k of RAM,
according to [46]).

### 2.8.1 Raspberry Pi

Raspberry Pis are single-board computers (SBCs) that can function as regular PCs. They are compact and inexpensive, yet offer a range of features such as a graphic driver. A mouse, keyboard, and screen can be connected to the device, and a Linux operating system can be installed on it [62]. Raspberry Pis can be programmed using various languages like Java, Python, or C++. Additionally, they incorporate WiFi and Bluetooth, enabling remote debugging of a device.

Advantages | Drawbacks
Fast: 700 MHz – 1.8 GHz processor | The processor is on a separate board
| and cannot be soldered directly onto the PCB (bulky)
Supports multiple programming lan- guages | Requires proper shutdown before power
| off
Incorporates WiFi and Bluetooth | More costly than other microcontrollers
Can execute complex calculations and applications | Consumes more power than regular
| MCUs
Can run the Robot Operating System
(ROS)

Table 2.13: Advantages and drawbacks of Raspberry Pi, largely based on [62].

2.8. MICROCONTROLLER | 35

Figure 2.17: The Raspberry Pi Mouse v3 is based on standard Raspberry Pi boards [5]

### 2.8.2 Arduino

Arduino boards are widespread MCUs in the maker’s community. They are inexpensive and easy to program through the dedicated Integrated Development Environment (IDE). These boards are ideal for quick prototypes and hacking projects. However, for more advanced projects, one can be limited by the IDE. Moreover, the devices do not integrate Bluetooth or WiFi. The microcontroller is a lot slower than on Raspberry Pi, with a common speed of 16 MHz [62]. From our analysis, the micromouse projects using Arduino are either beginner projects or ones meant for educational purposes.

Advantages | Drawbacks
Very inexpensive | Processor is on a separate board and
| cannot be soldered directly on the PCB (voluminous)
Easy to program through the IDE (in C or C++) | The IDE can be limiting
Low power | No WiFi or Bluetooth directly inte-
| grated

Table 2.14: Advantages and drawbacks of Arduino boards, widely based on [62].

36 | CHAPTER 2. STATE OF THE ART

### 2.8.3 STM32

STM32 microcontrollers appear to be the most widely used in intermediate and advanced micromouse projects (6 out of 10 projects studied). They are also equipped with ARM processors, like the Raspberry Pi boards. These microcontrollers have a faster clock than most Arduino boards, which means that they will perform the same calculations a lot quicker. Generally, the MCU will be directly soldered on the micromouse PCB, which allows for a significant gain of space. STM32 microcontrollers can also be programmed through the Arduino IDE, if desired [55]. This allows for a more powerful microcontroller, while still being able to program it very easily.

Advantages | Drawbacks
Powerful and cheap | Can be more difficult to program and
| understand, because it is more complex
| than Arduino
Faster clock than Arduino
Component can be soldered directly on PCB (small)

Table 2.15: Advantages and drawbacks of STM32 chips.

### 2.8.4 ESP32

ESP32 microcontrollers have emerged in the past few years and have become increasingly popular because of their versatility. The chips directly integrate WiFi and Bluetooth, which makes them ideal for IoT devices, or remotely controlled robots, for example. Moreover, ESP32 microcontrollers provide a lot more stack and flash than Arduinos, while still being compatible with the Arduino environment, which provides access to a multitude of libraries [64]. ESP32s have a large number of GPIO pins, and support multiple ADCs. All GPIO pins support interrupts, which is really useful in a micromouse project [28].

Advantages | Drawbacks
Powerful and cheap | Processor cannot be directly soldered on
| the micromouse PCB
Supported by the Arduino framework
Integrates WiFi and Bluetooth, some
modules have a removable antenna Dual core

Table 2.16: Advantages and drawbacks of ESP32 chips.

2.9. BREAKTHROUGHS OF MICROMOUSE CONTESTS | 37

## 2.9 Breakthroughs of Micromouse Contests

Throughout the years of the micromouse contests, some inventions stood out and spread among most of the competition winning robots. In the following sections, we present some of these revolutionary designs.

### 2.9.1 Handling Diagonals

Some sections of the micromouse mazes can be composed of multiple very short turns one after the other. A micromouse with a basic software would deal with these turns by moving forward, then stopping, then turning 90◦
, before finally re-accelerating for the next short segment. This approach is really inefficient, because the mouse never accelerates to its full speed. However, by building the mouse small enough, it can run down this part of the maze along a diagonal, hence hugely reducing the numbers of turns, as well as the total length of the path. This allows to solve the maze a lot faster. An example of a maze solution using diagonals is shown in Figure 2.18.

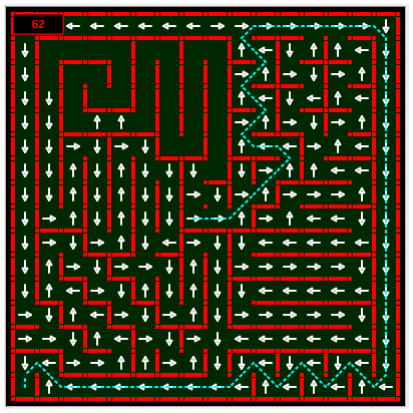
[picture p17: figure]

Figure 2.18: Example of a resolution of a maze using diagonals [41]

38 | CHAPTER 2. STATE OF THE ART
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

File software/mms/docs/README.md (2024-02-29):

# mms: Micromouse simulator

Open-source tool to simulate a micromouse: https://github.com/mackorone/mms-c?tab=readme-ov-file

## Using the C simulator for windows

### Configure new simulation

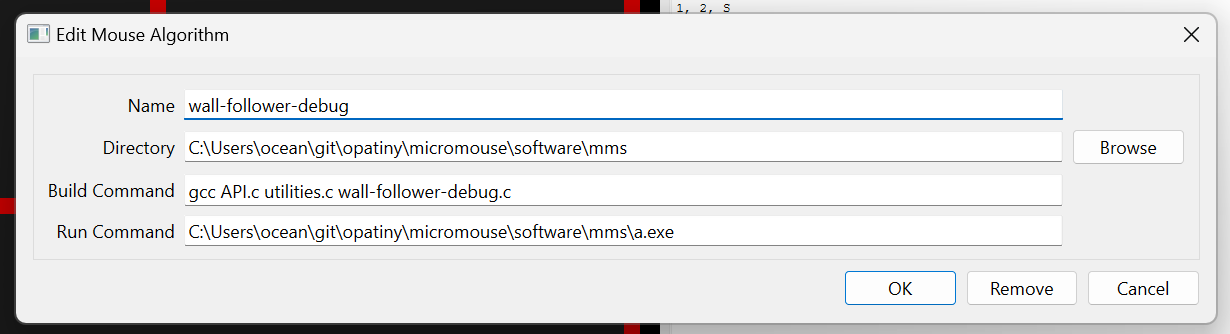
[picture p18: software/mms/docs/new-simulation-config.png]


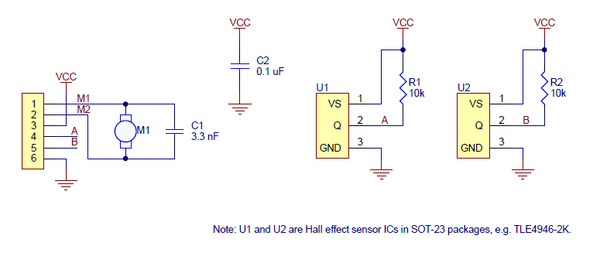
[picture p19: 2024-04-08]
docs/datasheets/images/encoders-schematic.jpg

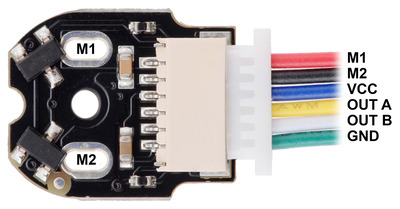
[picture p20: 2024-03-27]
docs/datasheets/images/encoder-pinout.jpg

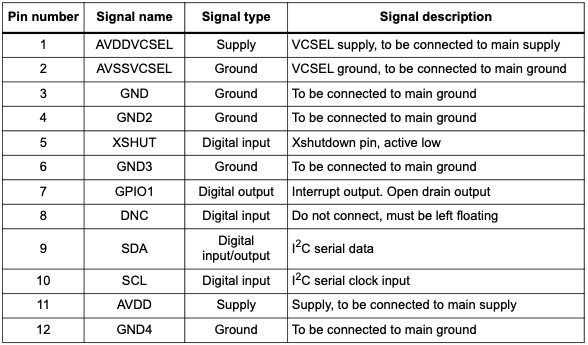
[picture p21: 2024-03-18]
docs/datasheets/images/vl53l1x-pin-description.png

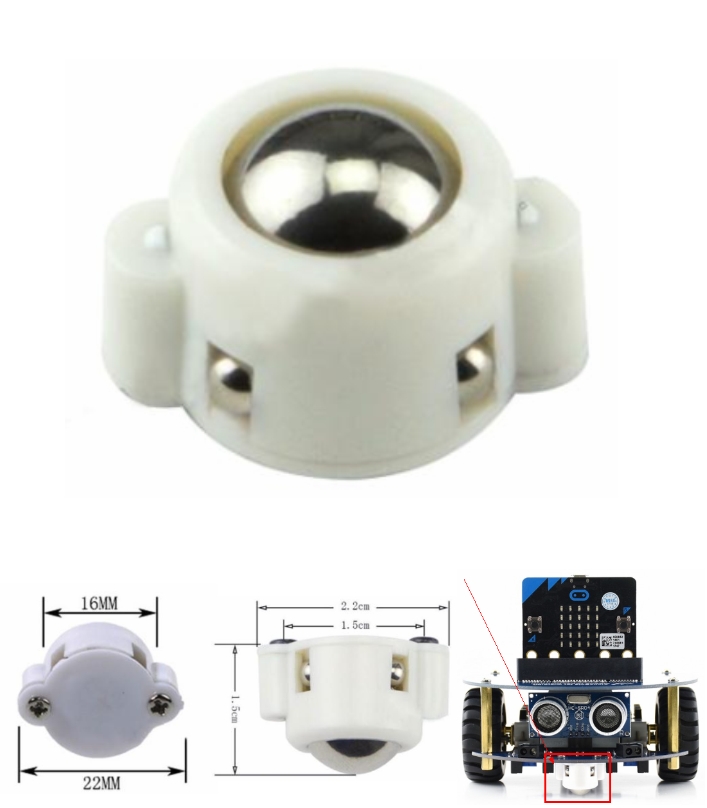
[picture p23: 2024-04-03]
docs/datasheets/images/caster-wheel-dimensions.jpeg

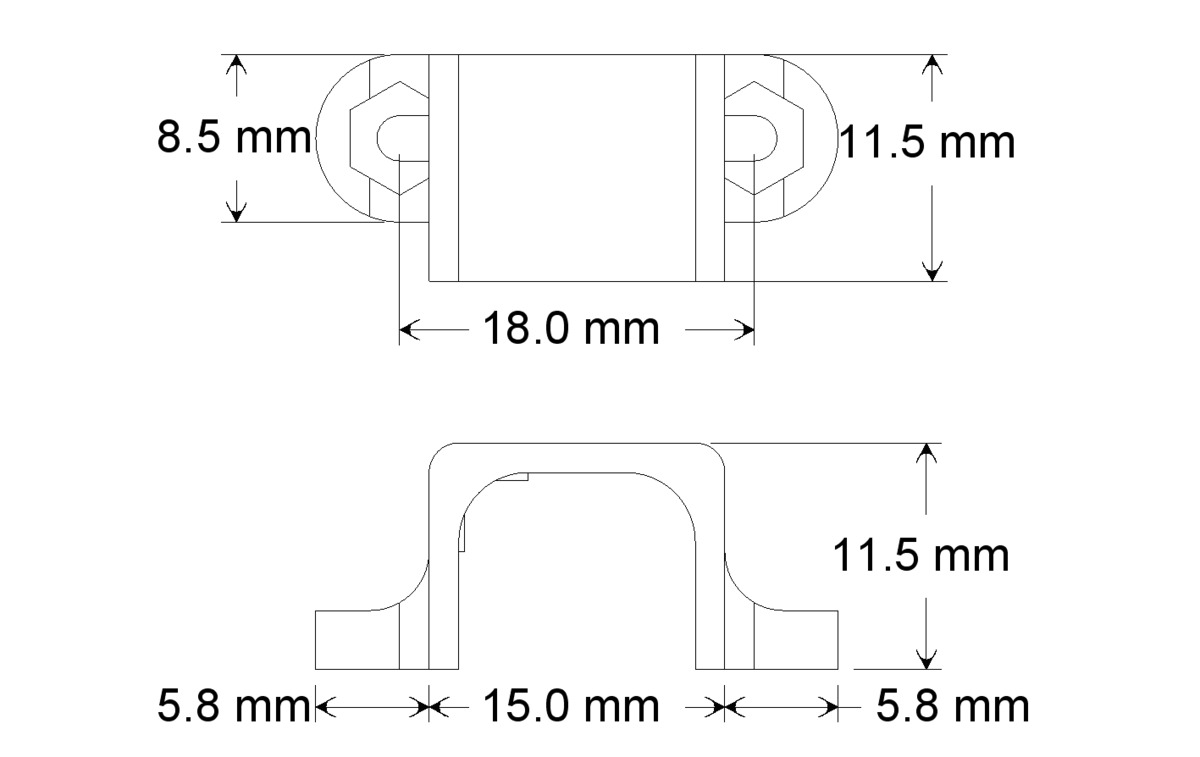
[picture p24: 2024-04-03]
docs/datasheets/images/polulu-bracket-gearmotor-dimensions.jpg

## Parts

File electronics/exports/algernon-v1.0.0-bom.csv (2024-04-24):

Reference, | Value, | Datasheet, | Footprint, | Qty, | DNP
BT1, | Battery, | ~, | footprints:LiPo_2S1P_Battery, | 1,
D1, | LED_VBAT, | ~, | LED_SMD:LED_1206_3216Metric_Pad1.42x1.75mm_HandSolder, | 1,
D2, | LED_3V3, | ~, | LED_SMD:LED_1206_3216Metric_Pad1.42x1.75mm_HandSolder, | 1,
DRV1, | DRV8833, | , | footprints:Polulu_DRV8833, | 1,
H1,H4, | Motor_holes, | ~, | footprints:Polulu_Micro_Gearmotor, | 2,
H2,H5, | Caster_wheel_holes, | ~, | footprints:caster_wheel_custom, | 2,
H3, | Bumper_front, | ~, | footprints:Micromouse_bumper, | 1,
H6, | Bumper_back, | ~, | footprints:Micromouse_bumper, | 1,
J1, | Left motor, | , | footprints:JST_SH_6pins, | 1,
J2, | Right motor, | , | footprints:JST_SH_6pins, | 1,
J3, | XT60-M, | , | footprints:AMASS_XT60-M, | 1,
LS1, | PKLCS1212E20A0-R1, | , | footprints:buzzer_double_footprint, | 1,
R1, | 20k, | ~, | Resistor_SMD:R_1206_3216Metric_Pad1.30x1.75mm_HandSolder, | 1,
R2, | 10k, | ~, | Resistor_SMD:R_1206_3216Metric_Pad1.30x1.75mm_HandSolder, | 1,
R3,R4, | 220, | ~, | Resistor_SMD:R_1206_3216Metric_Pad1.30x1.75mm_HandSolder, | 2,
R5, | 1k, | ~, | Resistor_SMD:R_1206_3216Metric_Pad1.30x1.75mm_HandSolder, | 1,
S1, | PTS526_SMG15_SMTR2_LFS, | , | footprints:SW_PTS526_SMG15_SMTR2_LFS, | 1,
U1, | ESP32-S3-DEVKITC-1U-N8R2, | , | footprints:XCVR_ESP32-S3-DEVKITC-1U-N8R2, | 1,
U2, | GY-521, | , | footprints:GY-521, | 1,
VL53L1X1, | Left, | , | footprints:TinyTronics_VL53L1X, | 1,
VL53L1X2, | Front-right, | , | footprints:TinyTronics_VL53L1X, | 1,
VL53L1X3, | Front-left, | , | footprints:TinyTronics_VL53L1X, | 1,
VL53L1X4, | Right, | , | footprints:TinyTronics_VL53L1X, | 1,
VL53L1X5, | Front, | , | footprints:TinyTronics_VL53L1X_header_front, | 1,

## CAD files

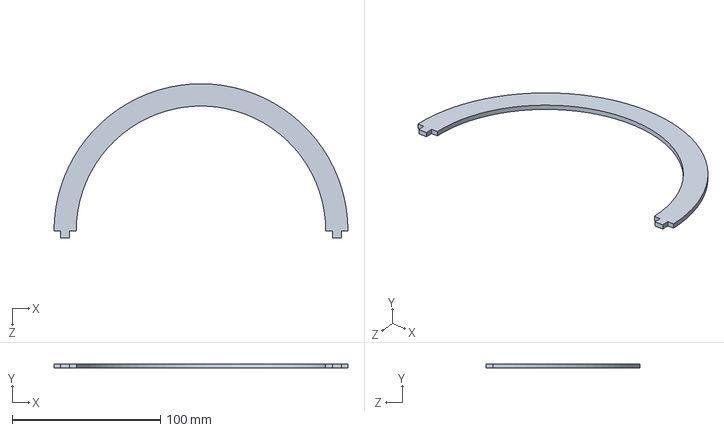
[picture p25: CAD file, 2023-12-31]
mechanics/maze/spacer-main.SLDPRT
198.0 x 3.00 x 104.0 mm

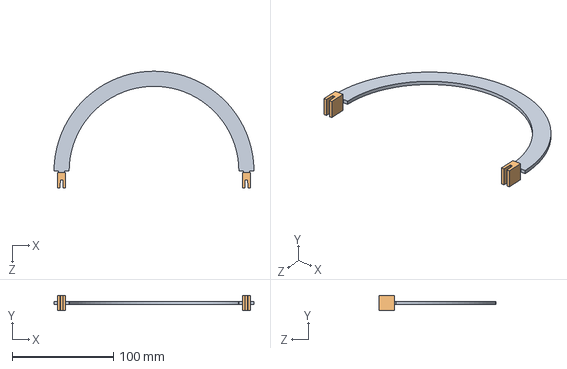
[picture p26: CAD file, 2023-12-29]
mechanics/maze/spacer.SLDASM
198.0 x 15.0 x 115.5 mm
spacer-main
spacer-fix x 2

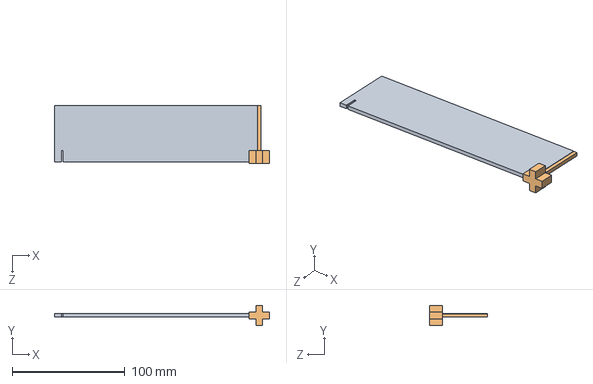
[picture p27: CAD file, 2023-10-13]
mechanics/maze/maze.SLDASM
190.6 x 18.0 x 51.5 mm
wall-1unit
corner

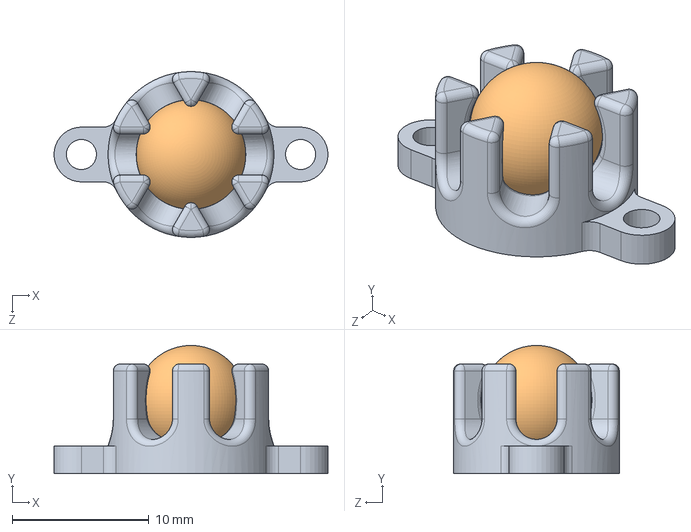
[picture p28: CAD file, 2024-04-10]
mechanics/solidworks/caster-wheel-custom.SLDASM
20.0 x 9.35 x 12.1 mm
caster-wheel-case
ball

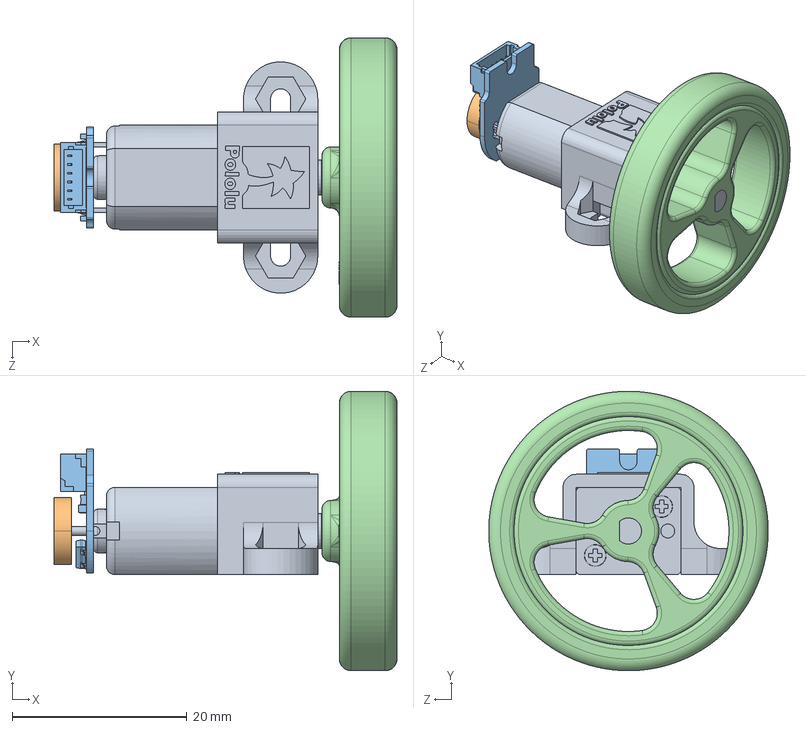
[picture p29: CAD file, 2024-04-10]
mechanics/solidworks/polulu-micromotor-assembly.SLDASM
39.3 x 32.0 x 32.0 mm
micro-metal-gearmotor-extended-with-1086-bracket
magnetic-encoder-disc-for-micro-metal-gearmotors
magnetic-encoder-with-side-entry-connector-for-micro-metal-gearmotors
pololu-wheel-32x7mm-black

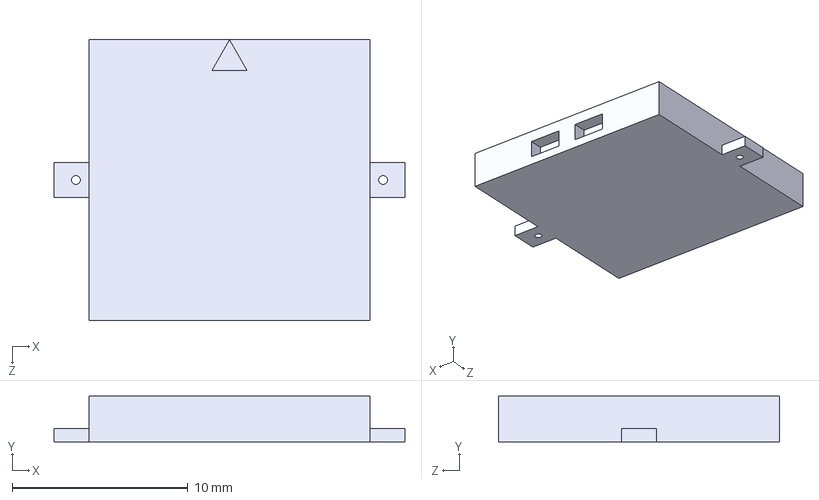
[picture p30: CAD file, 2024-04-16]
electronics/3dModels/KMTG1612.step
20.0 x 2.60 x 16.0 mm

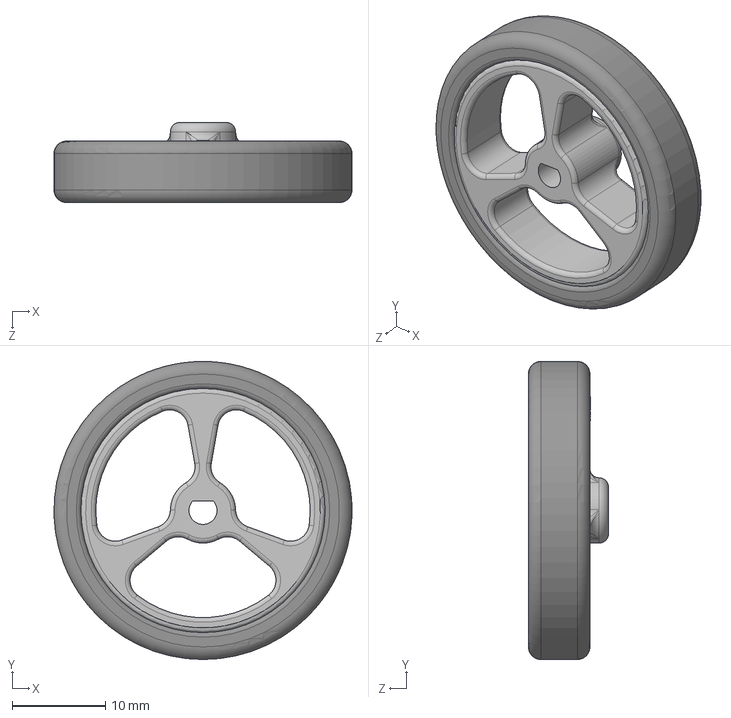
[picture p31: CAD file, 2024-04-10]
mechanics/internet-step/pololu-wheel-32x7mm-black.step
32.0 x 32.0 x 8.60 mm

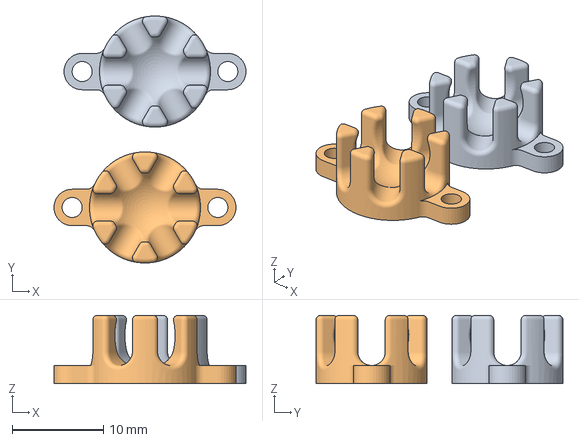
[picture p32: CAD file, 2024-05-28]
mechanics/manufacturing/prusaSlicer/caster-wheel-case.3mf
21.1 x 27.1 x 7.50 mm
caster-wheel-case-8.2mm.STL x 2

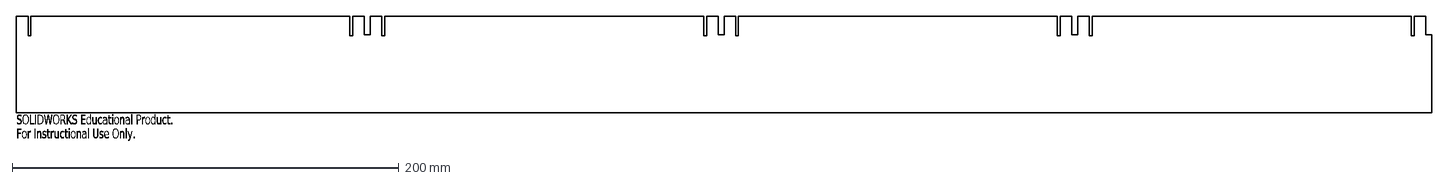
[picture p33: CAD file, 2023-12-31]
mechanics/maze/exports/dxf/wall-4units.DXF
SOLIDWORKS Educational Product.
For Instructional Use Only.

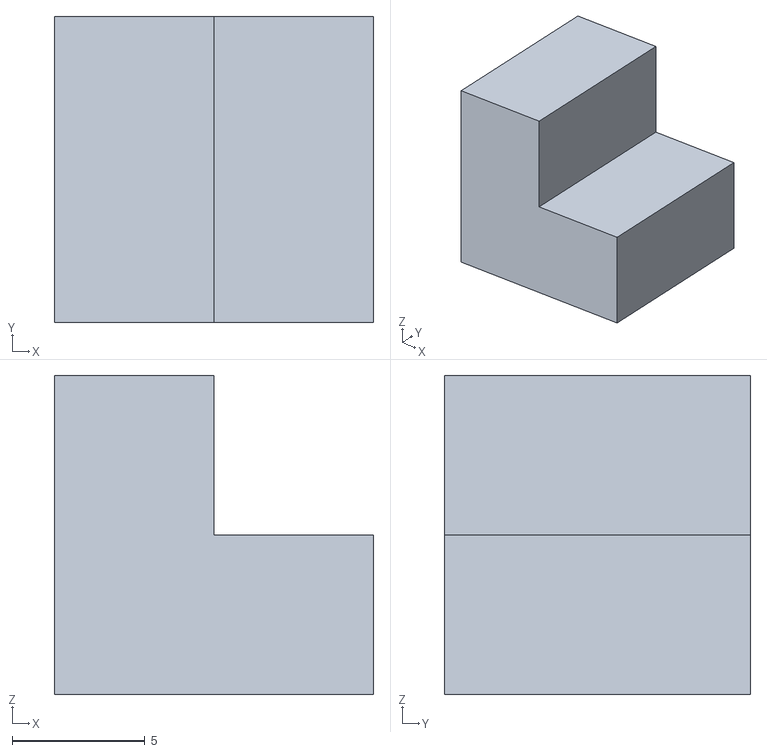
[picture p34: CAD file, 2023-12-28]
mechanics/maze/exports/stl/corner-angle-s017-e007.STL
12.0 x 11.5 x 12.0

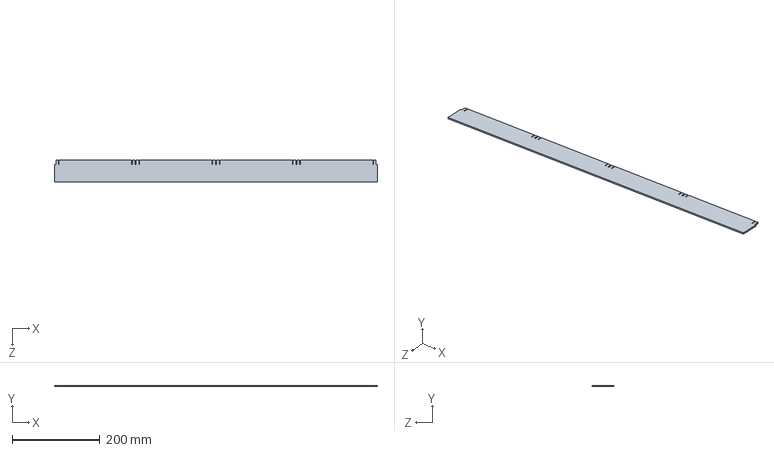
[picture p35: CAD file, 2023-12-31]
mechanics/maze/wall.SLDPRT
735.0 x 3.00 x 50.0 mm

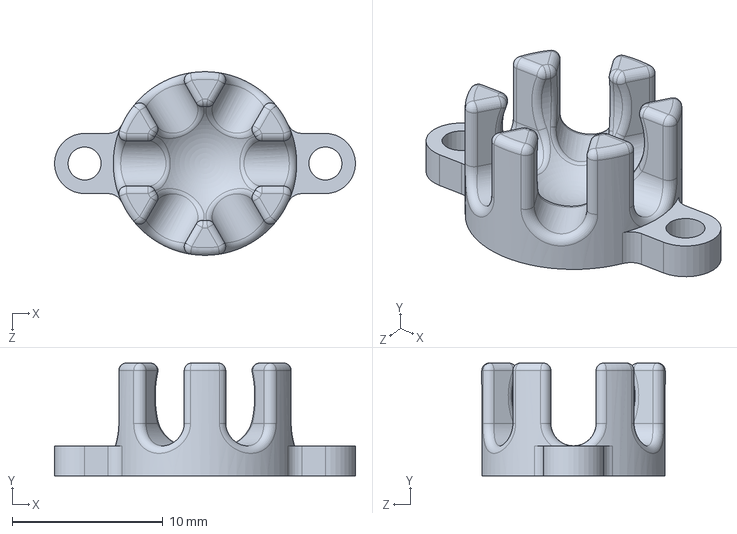
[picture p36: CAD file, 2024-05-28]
mechanics/solidworks/caster-wheel-case.SLDPRT
20.0 x 7.50 x 12.2 mm

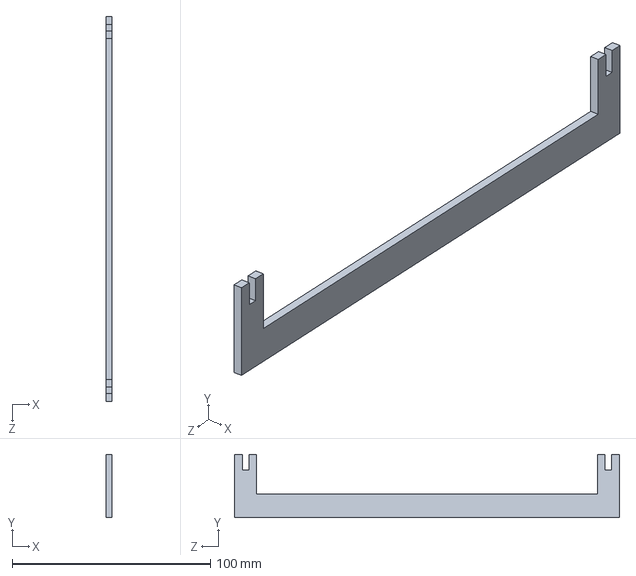
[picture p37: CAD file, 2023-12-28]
solidworks/maze/spacer.SLDPRT
3.00 x 32.0 x 194.4 mm

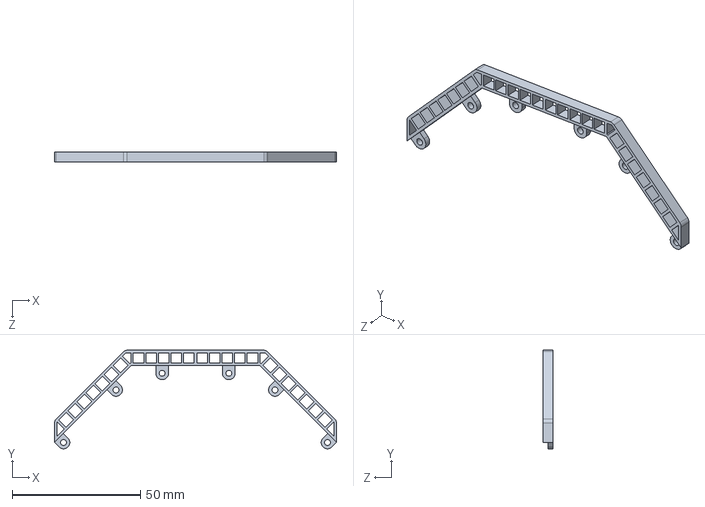
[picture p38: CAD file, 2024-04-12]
electronics/3dModels/bumper.STEP
110.0 x 38.5 x 4.00 mm

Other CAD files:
mechanics/solidworks/exports/stl/caster-wheel-case-8.2mm.STL
mechanics/internet-step/micro-metal-gearmotor-extended-with-1086-bracket.step
mechanics/manufacturing/prusaSlicer/bumper.3mf
mechanics/maze/exports/dxf/wall-4units-bothEnds.DXF
electronics/3dModels/GY-521.stp
electronics/3dModels/JST_SH_6pins.step
electronics/3dModels/PKLCS1212E20A0-R1.step
electronics/3dModels/PTS526_SMG15_SMTR2_LFS.step
electronics/3dModels/VL53l1X-noHoles.STEP
electronics/3dModels/VL53l1X.STEP
electronics/3dModels/XT60-M.step
electronics/3dModels/caster ball wheel.STEP
electronics/3dModels/caster-wheel-custom.STEP
electronics/3dModels/caster-wheel-spacer.STEP
electronics/3dModels/drv8833-dual-motor-driver-carrier.step
mechanics/internet-step/magnetic-encoder-disc-for-micro-metal-gearmotors.step
mechanics/internet-step/magnetic-encoder-with-side-entry-connector-for-micro-metal-gearmotors.step
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

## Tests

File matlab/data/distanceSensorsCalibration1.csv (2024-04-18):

left | front
0 | 21
55 | 65
109 | 122
147 | 165
182 | 168
203 | 269
231 | 310
232 | 260
217 | 407
184 | 444

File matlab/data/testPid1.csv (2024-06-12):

time | targetSpeed | leftSpeed | leftCommand | rightSpeed | rightCommand
39780 | 200 | 0.00 | 2 | 0.00 | 2
39791 | 200 | 0.00 | 3 | 0.00 | 3
39802 | 200 | 0.00 | 4 | 0.00 | 4
39813 | 200 | 0.00 | 5 | 0.00 | 5
39824 | 200 | 0.00 | 6 | 0.00 | 6
39835 | 200 | 0.00 | 7 | 0.00 | 7
39846 | 200 | 0.00 | 8 | 0.00 | 8
39857 | 200 | 0.00 | 9 | 0.00 | 9
39868 | 200 | 0.00 | 10 | 0.00 | 10
39879 | 200 | 0.00 | 11 | 0.00 | 11
39890 | 200 | 0.00 | 12 | 0.00 | 12
39901 | 200 | 0.00 | 13 | 0.00 | 13
39912 | 200 | 0.00 | 14 | 0.00 | 14
39923 | 200 | 0.00 | 15 | 0.00 | 15
39934 | 200 | 0.00 | 16 | 0.00 | 16
39945 | 200 | 0.00 | 17 | 0.00 | 17
39956 | 200 | 0.00 | 18 | 0.00 | 18
39967 | 200 | 0.00 | 19 | 0.00 | 19
39978 | 200 | 0.00 | 20 | 0.00 | 20
39989 | 200 | 0.00 | 21 | 0.00 | 21
40000 | 200 | 0.00 | 22 | 0.00 | 22
40011 | 200 | 0.00 | 23 | 0.00 | 23
40022 | 200 | 0.00 | 24 | 0.00 | 24
40033 | 200 | 0.00 | 25 | 0.00 | 25
40044 | 200 | 0.00 | 26 | 0.00 | 26
40055 | 200 | 0.00 | 27 | 0.00 | 27
40066 | 200 | 0.00 | 28 | 0.00 | 28
40077 | 200 | 0.00 | 29 | 0.00 | 29
40088 | 200 | 0.00 | 30 | 0.00 | 30
40099 | 200 | 0.00 | 31 | 0.00 | 31
40110 | 200 | 0.00 | 32 | 0.00 | 32
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

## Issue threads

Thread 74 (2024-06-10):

Write theory chapter

opatiny, 2024-06-10:
- [x] motors dimensionning
- [x] PID
- [x] odometry
- [x] diff drive
- [x] speed calibration

Closed 2024-08-06.

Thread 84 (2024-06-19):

Fix push button making device reboot

opatiny, 2024-06-19:
That happened when all the tasks were up at the same time.

Closed 2024-08-16.

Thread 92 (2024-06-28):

Add modes print utility

opatiny, 2024-06-28:
utility to print robot modes, buzzer modes, etc to help user

(md) debug modes
(mb) buzzer modes
(mr) robot modes
(ml) RGB led modes
...

Closed 2024-08-06.

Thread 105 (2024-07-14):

Write software chapter

opatiny, 2024-07-14:
- [x] prog environment
- [x] base project
- [x] multitasking
- [x] state
- [x] encoding and speed measurement
- [x] odometry
- [x] speed calibration
- [x] motor control
- [x] robot speed control
- [x] serial interface
- [x] wifi debug interface

Closed 2024-08-07.

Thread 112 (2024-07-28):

Check and fix report formatting

opatiny, 2024-07-28:
- [x] intro
- [x] state of the art
- [x] solutions
- [x] theory
- [x] electronics
- [x] pcb
- [x] mechanics
- [x] maze
- [x] software
- [x] results
- [x] improvements
- [x] conclusions
- [x] annexes

opatiny, 2024-08-10:
Here are a convention that can be used for the formatting: https://oreillymedia.github.io/production-resources/styleguide/

Closed 2024-08-15.

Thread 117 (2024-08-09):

Fix grammar

opatiny, 2024-08-09:
- [x] beginning
- [x] introduction
- [x] state of the art
- [x] solutions
- [x] theory
- [x] electronics
- [x] PCB design
- [x] mechanical design
- [x] maze
- [x] software
- [x] results and improvements
- [x] conclusions

Closed 2024-08-16.

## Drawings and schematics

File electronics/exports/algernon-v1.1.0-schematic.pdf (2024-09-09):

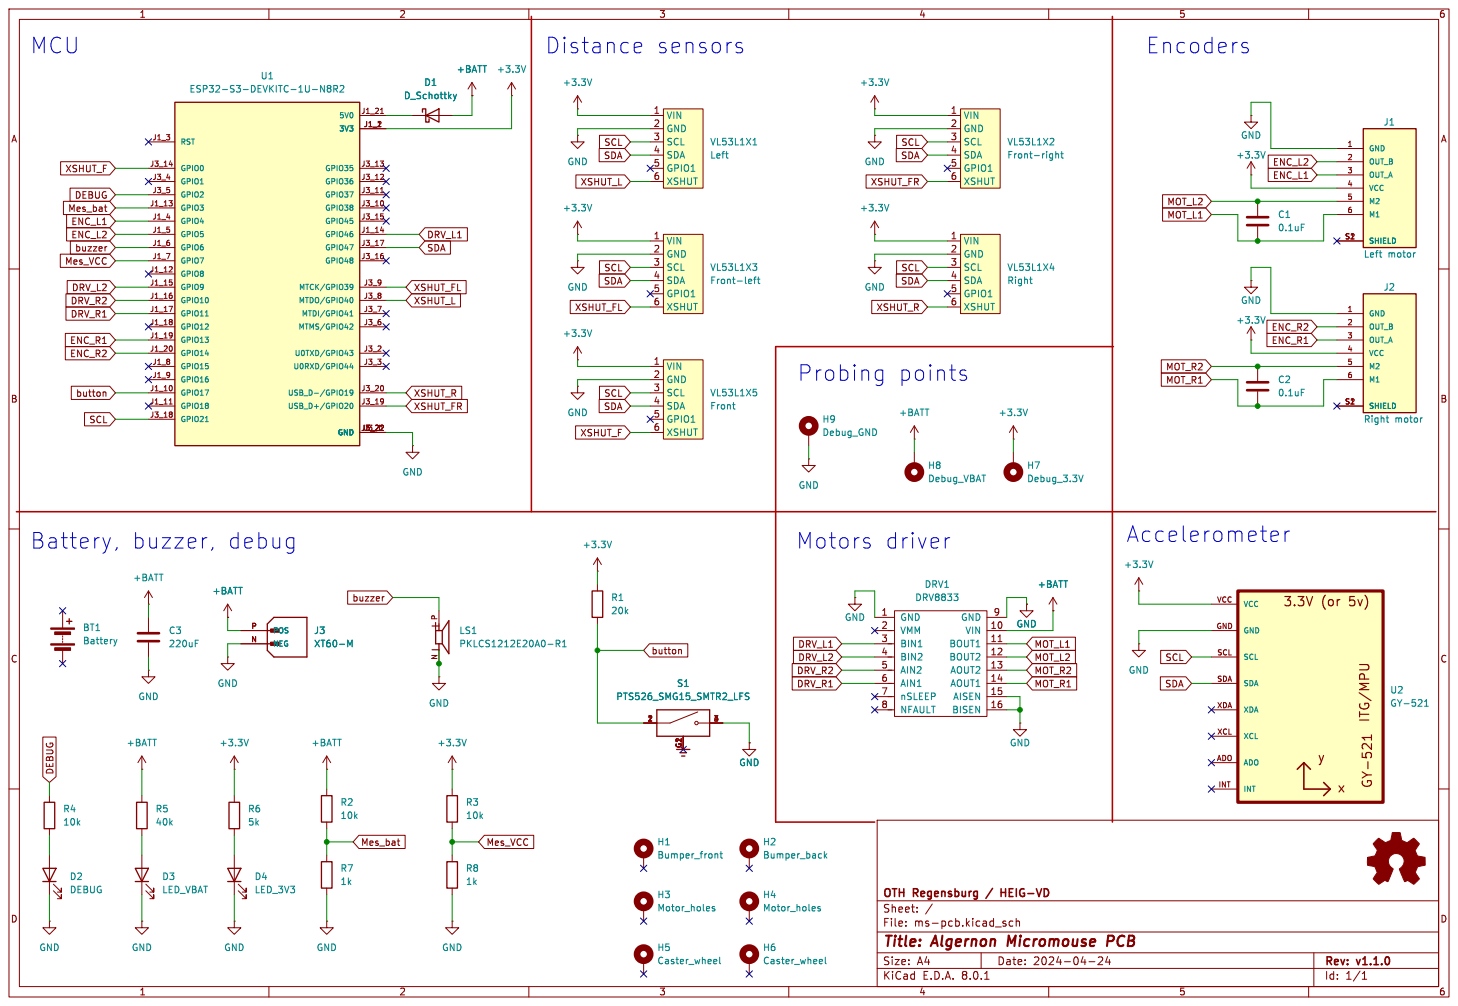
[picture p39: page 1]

Id: 1/1 Title: Algernon Micromouse PCB

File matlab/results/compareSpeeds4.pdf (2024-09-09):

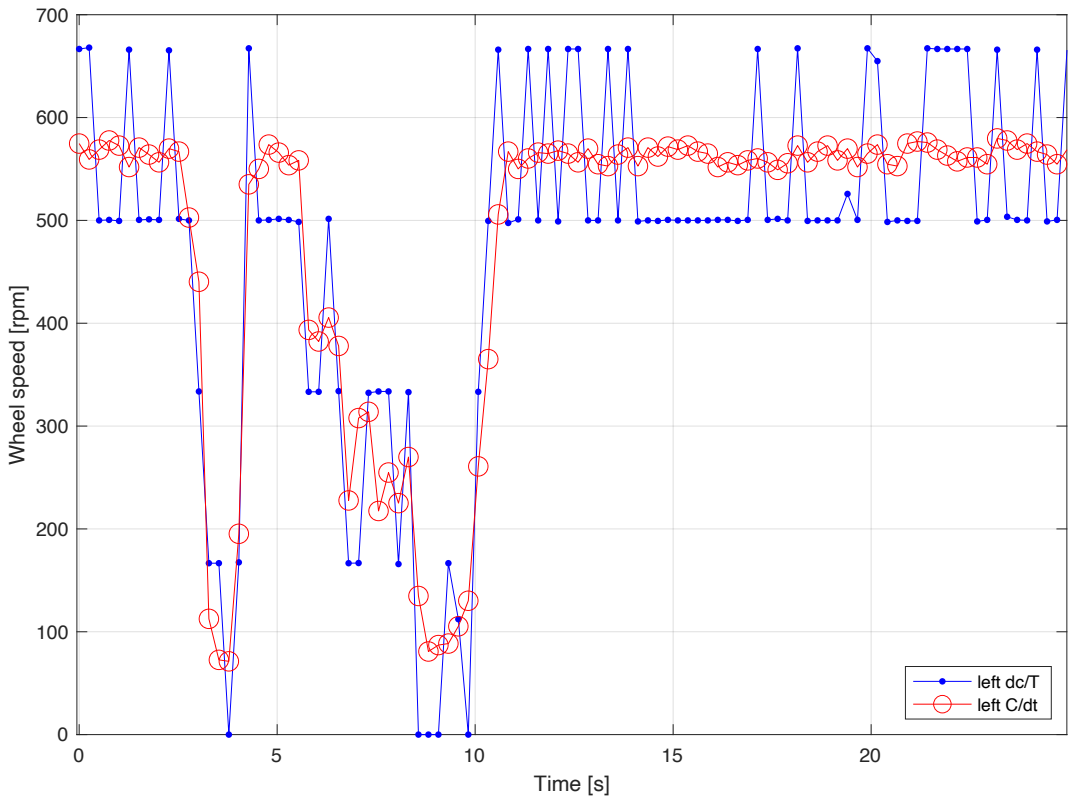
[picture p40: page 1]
Time [s]; left dc/T left C/dt

Wheel speed [rpm]

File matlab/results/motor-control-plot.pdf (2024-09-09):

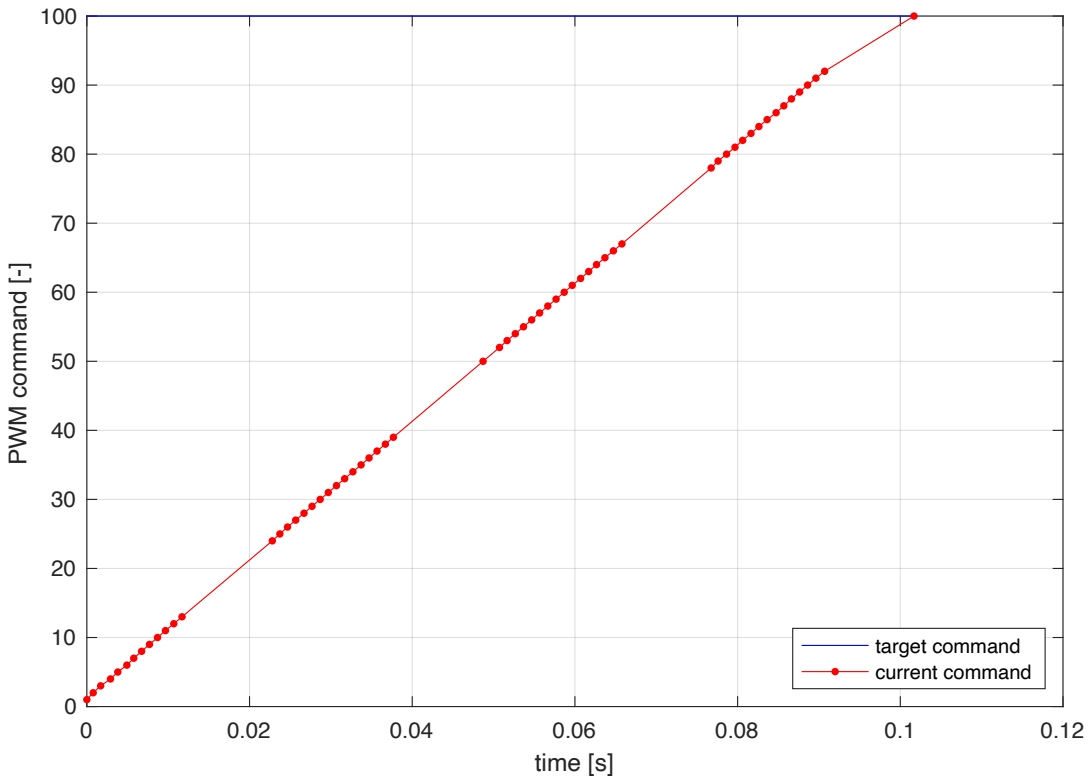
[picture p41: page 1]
time [s]; PWM command [-]; target command current command

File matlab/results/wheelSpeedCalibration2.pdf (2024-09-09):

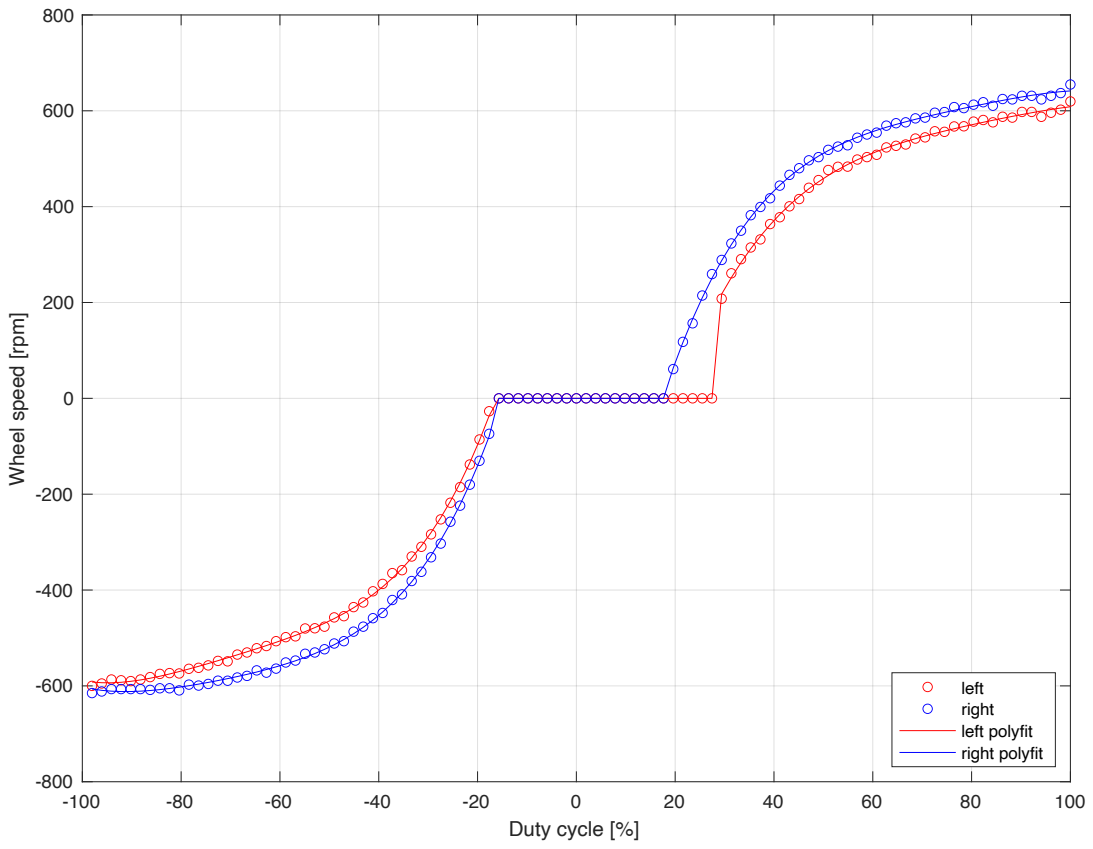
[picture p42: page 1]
Duty cycle [%]; left right left polyfit right polyfit

Wheel speed [rpm]

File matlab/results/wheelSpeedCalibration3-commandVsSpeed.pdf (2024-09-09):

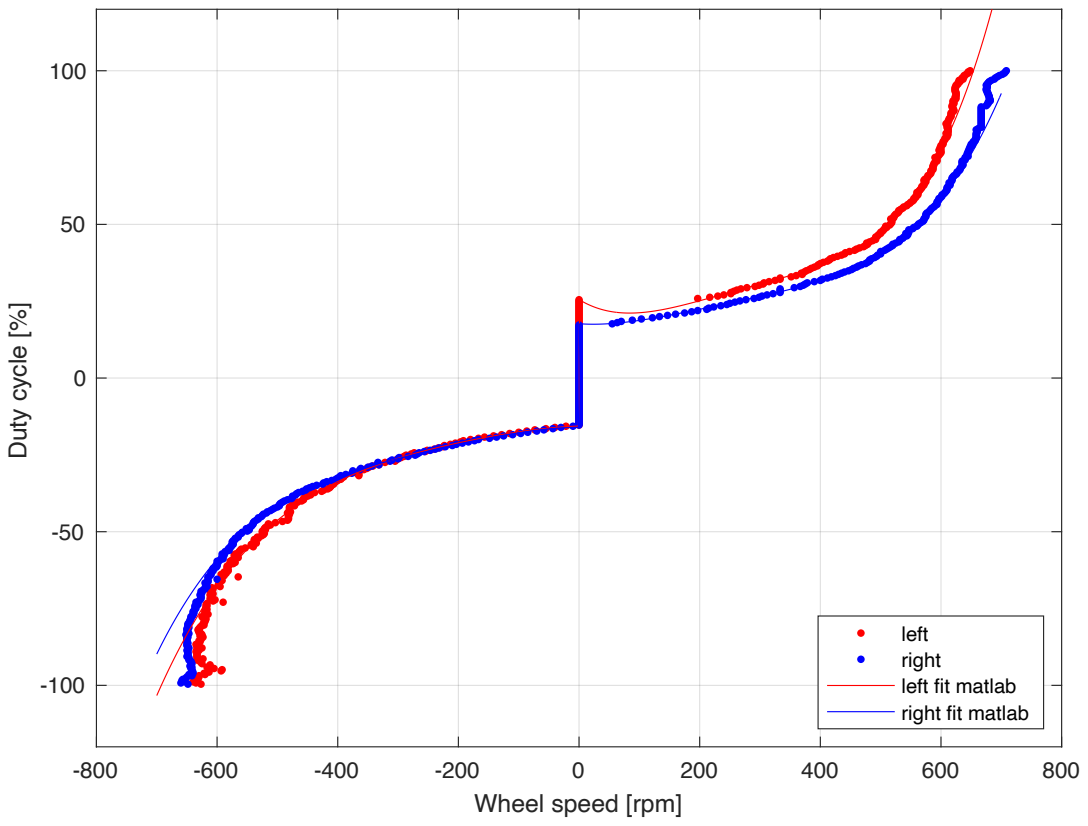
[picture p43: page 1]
Duty cycle [%]

left right left fit matlab

right fit matlab

Wheel speed [rpm]

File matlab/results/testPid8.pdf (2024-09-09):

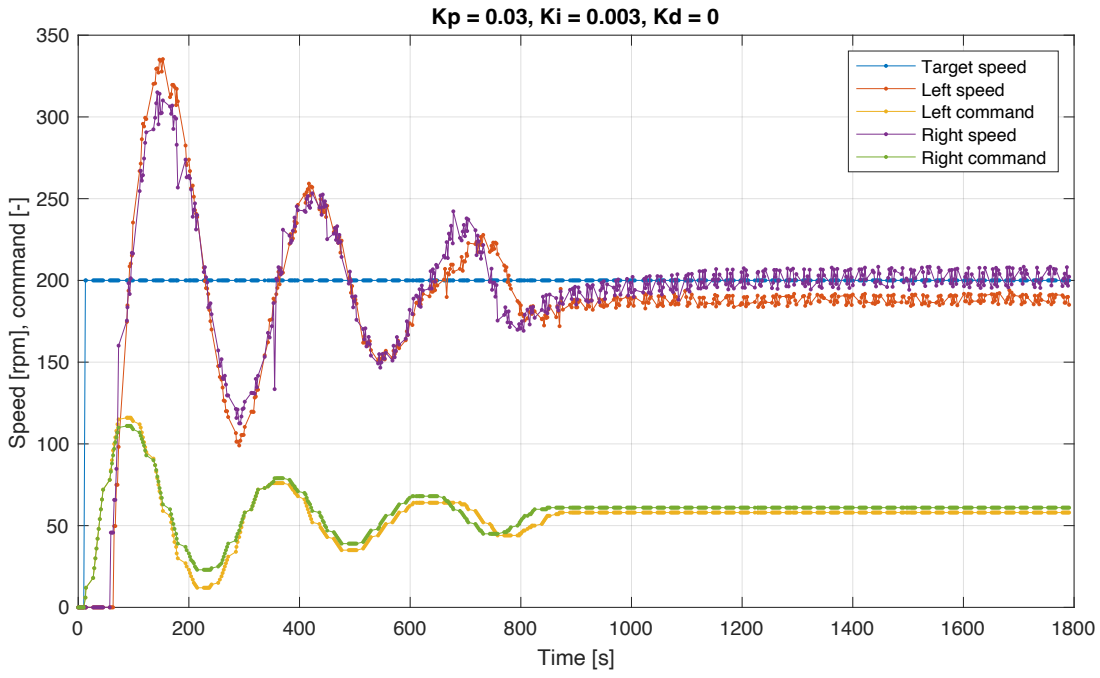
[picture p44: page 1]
Time [s]

Target speed Left speed Left command

Right speed Right command

Speed [rpm], command [-]

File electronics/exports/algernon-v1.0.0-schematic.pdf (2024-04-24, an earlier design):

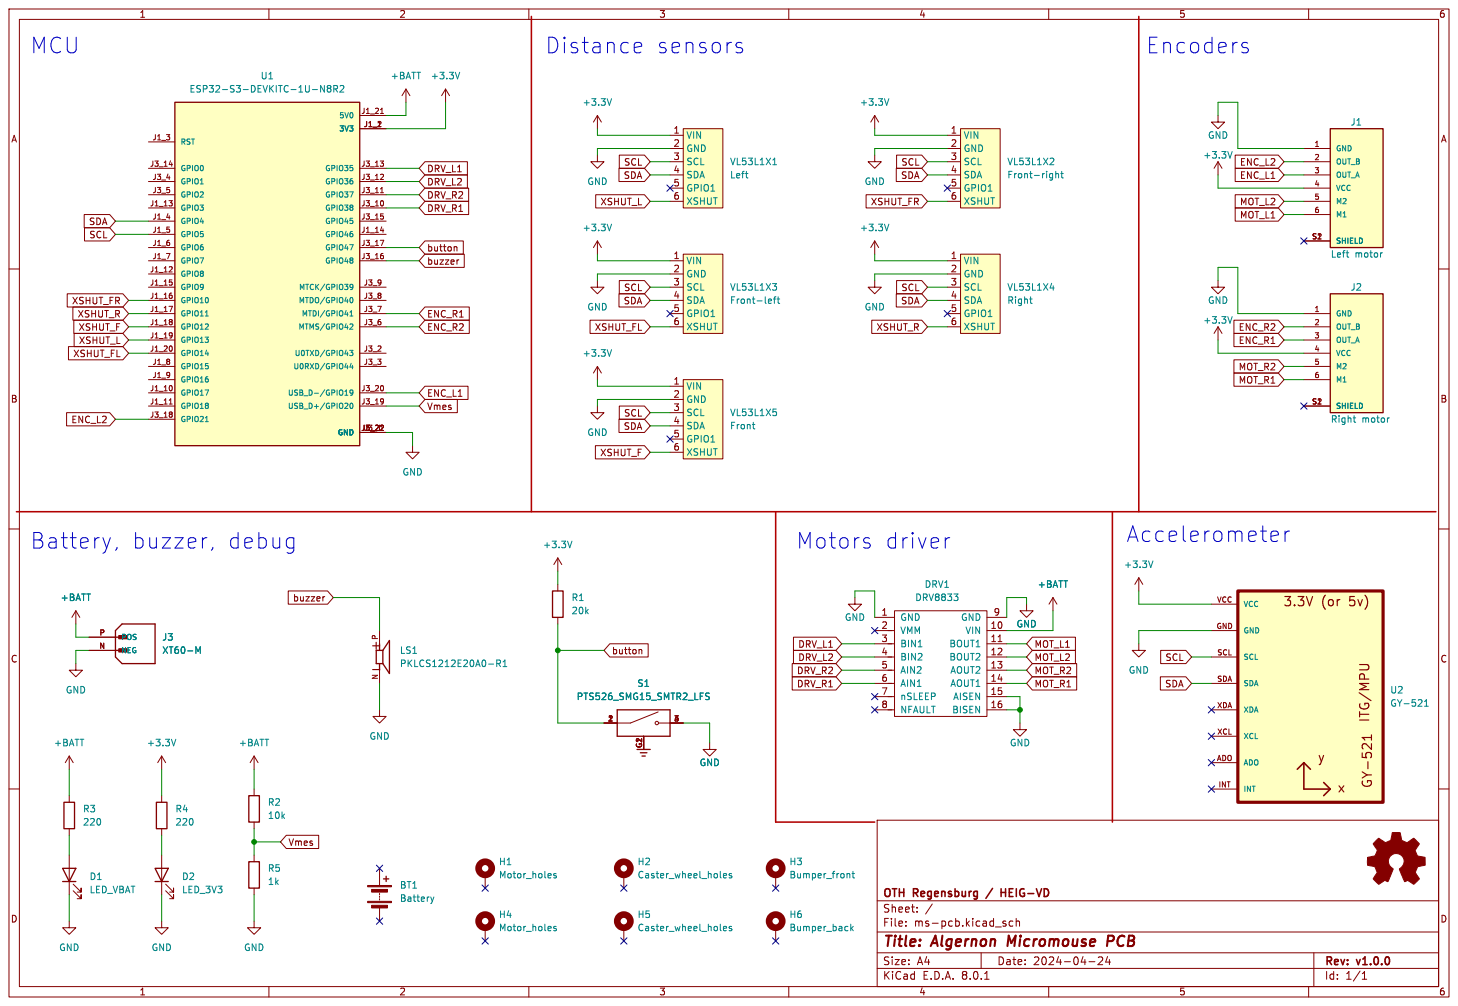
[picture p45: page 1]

Id: 1/1 Title: Algernon Micromouse PCB

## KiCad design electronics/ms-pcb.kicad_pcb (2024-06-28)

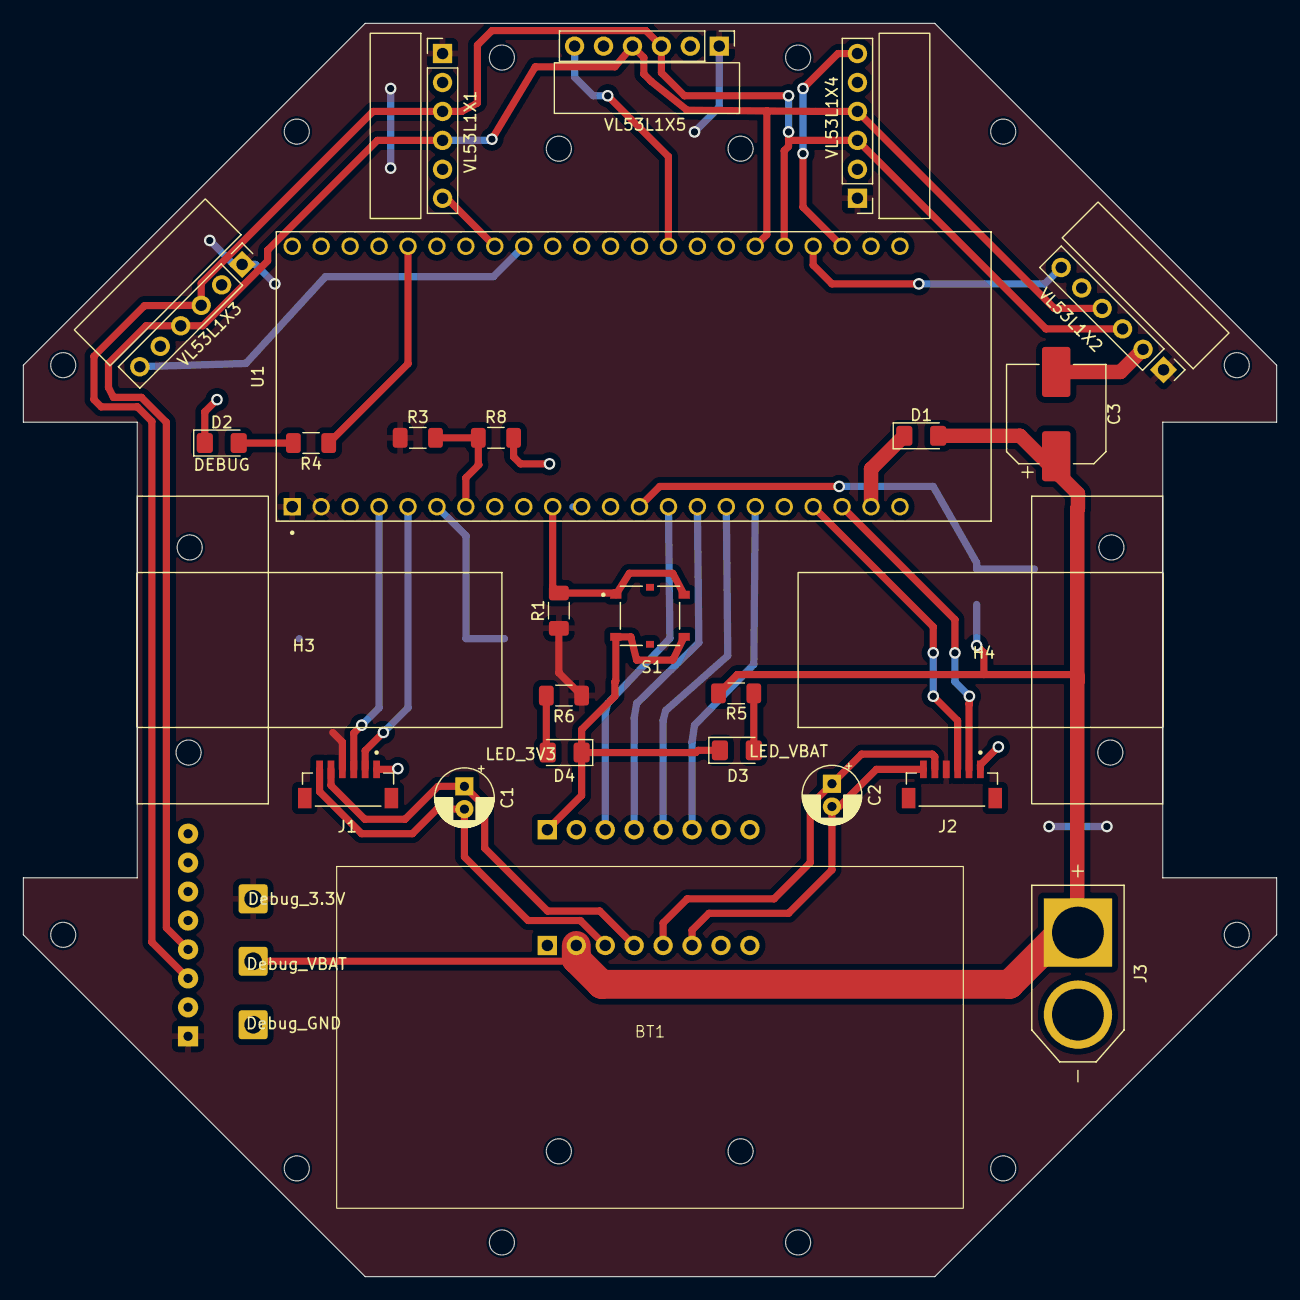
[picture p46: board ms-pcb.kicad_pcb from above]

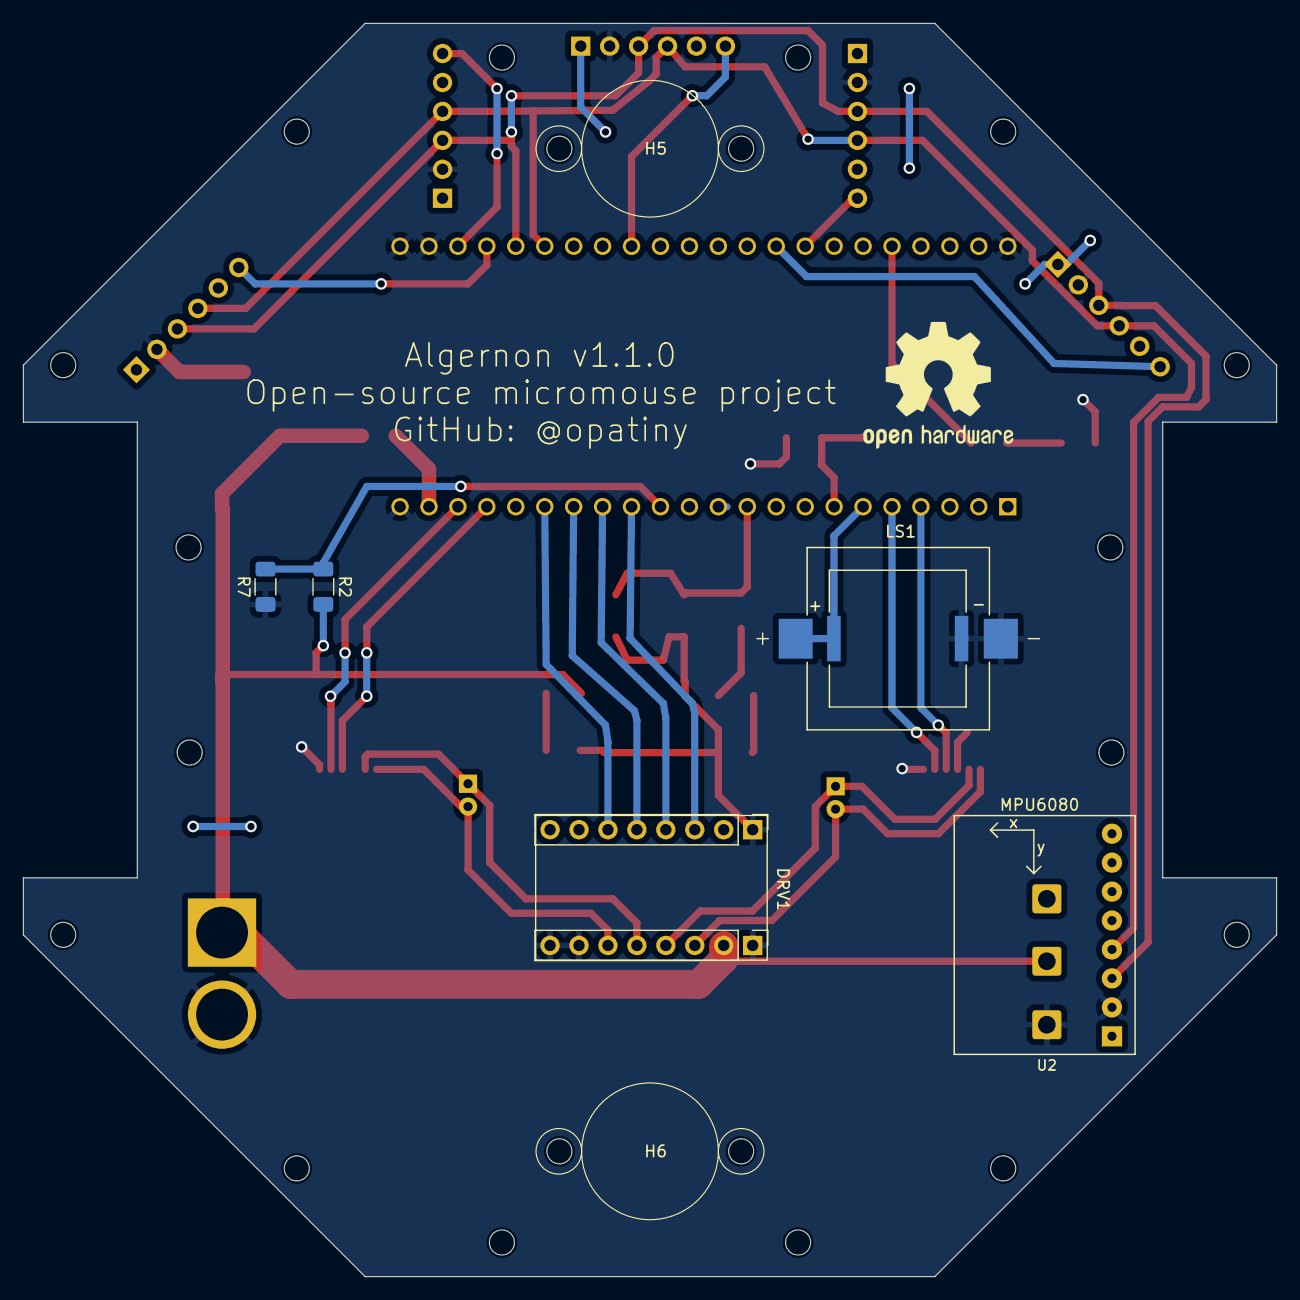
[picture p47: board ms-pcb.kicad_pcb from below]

Board: 2 copper layers, 110.0 x 110.0 mm, 38 parts (7 on the bottom side), 31 nets.

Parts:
BT1: Battery; LiPo_2S1P_Battery
C1, C2: 0.1uF; CP_Radial_D5.0mm_P2.00mm
C3: 220uF; CP_Elec_8x10.5
D1: D_Schottky; D_1206_3216Metric_Pad1.42x1.75mm_HandSolder
D2: DEBUG; LED_1206_3216Metric_Pad1.42x1.75mm_HandSolder
D3: LED_VBAT; LED_1206_3216Metric_Pad1.42x1.75mm_HandSolder
D4: LED_3V3; LED_1206_3216Metric_Pad1.42x1.75mm_HandSolder
DRV1: DRV8833; Polulu_DRV8833
H1: Bumper_front; Micromouse_bumper
H2: Bumper_back; Micromouse_bumper
H3, H4: Motor_holes; Polulu_Micro_Gearmotor
H5, H6: Caster_wheel; caster_wheel_custom
H7: Debug_3.3V; SolderWire-0.75sqmm_1x01_D1.25mm_OD2.3mm
H8: Debug_VBAT; SolderWire-0.75sqmm_1x01_D1.25mm_OD2.3mm
H9: Debug_GND; SolderWire-0.75sqmm_1x01_D1.25mm_OD2.3mm
J1: Left motor; JST_SH_6pins
J2: Right motor; JST_SH_6pins
J3: XT60-M; AMASS_XT60-M
LS1: PKLCS1212E20A0-R1; buzzer_double_footprint
R1: 20k; R_1206_3216Metric_Pad1.30x1.75mm_HandSolder
R2, R3, R4: 10k; R_1206_3216Metric_Pad1.30x1.75mm_HandSolder
R5: 40k; R_1206_3216Metric_Pad1.30x1.75mm_HandSolder
R6: 5k; R_1206_3216Metric_Pad1.30x1.75mm_HandSolder
R7, R8: 1k; R_1206_3216Metric_Pad1.30x1.75mm_HandSolder
S1: PTS526_SMG15_SMTR2_LFS; SW_PTS526_SMG15_SMTR2_LFS
U1: ESP32-S3-DEVKITC-1U-N8R2; XCVR_ESP32-S3-DEVKITC-1U-N8R2
U2: GY-521
VL53L1X1: Left; TinyTronics_VL53L1X
VL53L1X2: Front-right; TinyTronics_VL53L1X
VL53L1X3: Front-left; TinyTronics_VL53L1X
VL53L1X4: Right; TinyTronics_VL53L1X
VL53L1X5: Front; TinyTronics_VL53L1X_header_front

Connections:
+3.3V: H7.1, J1.4 (VCC), J2.4 (VCC), R1.1, R3.1, R6.1, U1.J1_1 (3V3), U1.J1_2 (3V3), U2.VCC, VL53L1X1.1 (VIN), VL53L1X2.1 (VIN), VL53L1X3.1 (VIN), VL53L1X4.1 (VIN), VL53L1X5.1 (VIN)
+BATT: C3.1, D1.2 (A), DRV1.10 (VIN), H8.1, J3.P (POS), R2.1, R5.1
DEBUG: R4.1, U1.J3_5 (GPIO2)
DRV_L1: DRV1.3 (BIN1), U1.J1_14 (GPIO46)
DRV_L2: DRV1.4 (BIN2), U1.J1_15 (GPIO9)
DRV_R1: DRV1.6 (AIN1), U1.J1_17 (GPIO11)
DRV_R2: DRV1.5 (AIN2), U1.J1_16 (GPIO10)
ENC_L1: J1.3 (OUT_A), U1.J1_4 (GPIO4)
ENC_L2: J1.2 (OUT_B), U1.J1_5 (GPIO5)
ENC_R1: J2.3 (OUT_A), U1.J1_19 (GPIO13)
ENC_R2: J2.2 (OUT_B), U1.J1_20 (GPIO14)
GND: C3.2, D2.1 (K), D3.1 (K), D4.1 (K), DRV1.1 (GND), DRV1.9 (GND), DRV1.15 (AISEN), DRV1.16 (BISEN), H9.1, J1.1 (GND), J2.1 (GND), J3.N (NEG), LS1.N, R7.2, R8.2, S1.3, S1.4, U1.J1_22 (GND), U1.J3_1 (GND), U1.J3_21 (GND), U1.J3_22 (GND), U2.GND, VL53L1X1.2 (GND), VL53L1X2.2 (GND), VL53L1X3.2 (GND), VL53L1X4.2 (GND), VL53L1X5.2 (GND)
MOT_L1: C1.2, DRV1.11 (BOUT1), J1.6 (M1)
MOT_L2: C1.1, DRV1.12 (BOUT2), J1.5 (M2)
MOT_R1: C2.2, DRV1.14 (AOUT1), J2.6 (M1)
MOT_R2: C2.1, DRV1.13 (AOUT2), J2.5 (M2)
Mes_VCC: R3.2, R8.1, U1.J1_7 (GPIO7)
Mes_bat: R2.2, R7.1, U1.J1_13 (GPIO3)
unnamed: D1.1 (K), U1.J1_21 (5V0)
unnamed: D2.2 (A), R4.2
unnamed: D3.2 (A), R5.2
unnamed: D4.2 (A), R6.2
SCL: U1.J3_18 (GPIO21), U2.SCL, VL53L1X1.3 (SCL), VL53L1X2.3 (SCL), VL53L1X3.3 (SCL), VL53L1X4.3 (SCL), VL53L1X5.3 (SCL)
SDA: U1.J3_17 (GPIO47), U2.SDA, VL53L1X1.4 (SDA), VL53L1X2.4 (SDA), VL53L1X3.4 (SDA), VL53L1X4.4 (SDA), VL53L1X5.4 (SDA)
XSHUT_F: U1.J3_14 (GPIO0), VL53L1X5.6 (XSHUT)
XSHUT_FL: U1.J3_9 (MTCK/GPIO39), VL53L1X3.6 (XSHUT)
XSHUT_FR: U1.J3_19 (USB_D+/GPIO20), VL53L1X2.6 (XSHUT)
XSHUT_L: U1.J3_8 (MTDO/GPIO40), VL53L1X1.6 (XSHUT)
XSHUT_R: U1.J3_20 (USB_D-/GPIO19), VL53L1X4.6 (XSHUT)
button: R1.2, S1.1, S1.2, U1.J1_10 (GPIO17)
buzzer: LS1.P, U1.J1_6 (GPIO6)

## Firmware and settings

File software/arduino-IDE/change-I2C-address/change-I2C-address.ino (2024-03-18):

/*
This example shows how to set up and read multiple VL53L1X sensors connected to
the same I2C bus. Each sensor needs to have its XSHUT pin connected to a
different Arduino pin, and you should change sensorCount and the xshutPins array
below to match your setup.

For more information, see ST's application note AN4846 ("Using multiple VL53L0X
in a single design"). The principles described there apply to the VL53L1X as
well.
*/

#include <Wire.h>
#include <VL53L1X.h>

#define ADDRESS 0x35

VL53L1X sensor;

void setup()
{
  Serial.begin(9600);
  while (!Serial) {}

  Wire.begin();

  sensor.setAddress(ADDRESS);
  Serial.print("New address set to 0x");
  Serial.println(sensor.getAddress(), HEX);
  sensor.startContinuous(50);
  Serial.println("Continuous sensing");
}

void loop()
{
  delay(1000);
  Serial.print(sensor.read());
  if (sensor.timeoutOccurred()) { Serial.print(" TIMEOUT"); }
  Serial.print('\t');
  Serial.println();
}

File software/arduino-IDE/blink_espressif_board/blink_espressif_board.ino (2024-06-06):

/*
  Blink

  Turns an LED on for one second, then off for one second, repeatedly.

  Most Arduinos have an on-board LED you can control. On the UNO, MEGA and ZERO
  it is attached to digital pin 13, on MKR1000 on pin 6. LED_BUILTIN is set to
  the correct LED pin independent of which board is used.
  If you want to know what pin the on-board LED is connected to on your Arduino
  model, check the Technical Specs of your board at:
  https://www.arduino.cc/en/Main/Products

  modified 8 May 2014
  by Scott Fitzgerald
  modified 2 Sep 2016
  by Arturo Guadalupi
  modified 8 Sep 2016
  by Colby Newman

  This example code is in the public domain.

  https://www.arduino.cc/en/Tutorial/BuiltInExamples/Blink
*/
#define LED 38

// the setup function runs once when you press reset or power the board
void setup() {
  Serial.begin(9600);
  while (!Serial) {}
  pinMode(LED, OUTPUT);
}

// the loop function runs over and over again forever
void loop() {
  Serial.println("high");
  digitalWrite(LED, HIGH);  // turn the LED on (HIGH is the voltage level)
  delay(1000);                      // wait for a second
    Serial.println("low");
  digitalWrite(LED, LOW);   // turn the LED off by making the voltage LOW
  delay(1000);                      // wait for a second
}

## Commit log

2023-10-08 sw: first maze model
    [corner-cross.STL, corner.SLDPRT, maze.SLDASM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]
2023-10-13 sw: add studs to corners
    [corner-T-stud.STL, corner-T.STL, corner-angle-stud.STL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]
2023-10-13 sw: working on maze corners
    [corner-all-4x.3mf, corner-straight-j13.STL, corner-straight-j15.STL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]
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2023-12-28 sw: adapt corner play
    [corner-T-s017-e007.STL, corner-T-stud.STL, corner-T.STL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]
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2023-12-28 refactor: move slicer files to manufacturing folder
    [corner-all-4x.3mf, corner-no-studs-4x.3mf, corner-studs-4x.3mf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]
2023-12-31 refactor: rename slicer to prusaSlicer
    [corner-all-4x.3mf, corner-no-studs-4x.3mf, corner-studs-4x.3mf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]
2023-12-31 sw: enhancing maze spacer
    [spacer-fix-w8.STL, spacer-fix.SLDPRT, spacer-fix.STL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]
2023-12-31 sw: export 4 units wall
    [spacer-old.SLDPRT, wall-1unit.SLDPRT, wall-4units-bothEnds.DXF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]
2024-01-01 chore: cleanup useless gcode
    [corner-all-4x.3mf, corner-no-studs-4x.3mf, corner-studs-4x.3mf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]
2024-01-20 manuf: working on corners
    [corner-all-4x.3mf, corner-all-64.3mf]
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2024-03-20 mec: add drv8833 3d model
    [drv8833-dual-motor-driver-carrier-step.step]
2024-03-21 docs: add esp pins attribution md
    [magnetic-encoder-disc-for-micro-metal-gearmotors.step, magnetic-encoder-with-side-entry-connector-for-micro-metal-gearmotors.step, magnetic-encoder-with-top-en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]
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2024-03-27 elec: add components ecad files and start PCB v0.1
    [JST_SH_6pins.step, PKLCS1212E20A0-R1.step, XT60-M.step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]
2024-03-27 refactor: delete solidworks folder
    [corner-T-s017-e007.STL, corner-angle-s017-e007.STL, corner-angle-s02-e01.STL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]
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2024-03-27 elec: first PCB schematic draft
    [ms-pcb.kicad_sch]
2024-04-03 elec: design some missing footprints
    [PTS526_SMG15_SMTR2_LFS.step, VL53l1X.IGS, VL53l1X.SLDPRT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]
2024-04-03 elec: start PCB layout
    [ms-pcb.kicad_pcb, ms-pcb.kicad_sch]
2024-04-04 elec: minor schematic fixes
    [ms-pcb.kicad_sch]
2024-04-05 matlab: analyse battery voltage
    [batteryVoltage1.csv, batteryVoltage2.csv, batteryVoltage3.csv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]
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2024-04-09 elec: add more 3D and link them to footprints
    [drv8833-dual-motor-driver-carrier.step, micro-metal-gearmotor-extended-with-1086-bracket.step, ms-pcb.kicad_pcb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]
2024-04-09 elec: add most 3D models
    Closes: #19
    [VL53l1X.STEP, ms-pcb.kicad_pcb, ms-pcb.kicad_sch]
2024-04-10 mec: add some step files
    [VL53l1X.IGS, VL53l1X.SLDPRT, magnetic-encoder-disc-for-micro-metal-gearmotors.step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]
2024-04-10 mec: start solidworks design
    [VL53l1X.SLDPRT, caster ball wheel.SLDPRT, caster ball wheel.STEP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]
2024-04-10 elec: add more 3D models and enhance layout
    [GY-521.stp, VL53l1X-noHoles.STEP, caster ball wheel.STEP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]
2024-04-10 mec: prusa slicer files
    [VL53l1X.IGS, VL53l1X.SLDPRT, caster-wheel-spacer.3mf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]
2024-04-10 mec: design custom caster wheel, bumper and pcb base
    [ball.SLDPRT, bumper.SLDPRT, bumper.STEP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]
2024-04-10 elec: enhance PCB v0.1 layout
    [caster-wheel-custom.STEP, ms-pcb.kicad_pcb, ms-pcb.kicad_sch]
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2024-04-12 elec: PCB layout wiring
    [bumper.STEP, ms-pcb.kicad_pcb, ms-pcb.kicad_sch]
2024-04-12 refactor: move manufacturing folder
    [caster-wheel-spacer.3mf, corner-all-64.3mf, spacer-fix.3mf]
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2024-04-12 refactor: remove useless folder ms-pcb
    [GY-521.stp, JST_SH_6pins.step, PKLCS1212E20A0-R1.step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]
2024-04-15 elec: minor PCB layout changes
    [ms-pcb.kicad_pcb]
2024-04-16 fix: finish PCB layout v1.0.0
    Closes: #10
    [KMTG1612.step, ms-pcb.kicad_pcb, ms-pcb.kicad_sch]
2024-04-17 fix: caster wheel
    Closes: #34
    [caster-wheel-case.3mf, caster-wheel-case.SLDPRT, caster-wheel-case.STL]
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2024-04-17 mec: design bumper springy
    [bumper-springy.SLDPRT, bumper-springy.STL, bumper.3mf]
2024-04-18 matlab: working on distance sensors calbration
    [distanceSensorsConstant1.csv]
2024-04-18 matlab: calibration of distance sensors
    [distanceSensorsCalibration1.csv]
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2024-04-24 elec: export schematic of pcb v1.0.0 as pdf
    [algernon-v1.0.0-bom.csv, ms-pcb.kicad_sch]
2024-04-26 matlab: encoders data script
    [batteryVoltage5.csv, encoders1.csv, encoders2.csv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]
2024-04-29 elec: change debug leds resistors values
    [ms-pcb.kicad_pcb]
2024-05-03 elec: start PCB v1.1.0
    [ms-pcb.kicad_pcb, ms-pcb.kicad_sch]
2024-05-03 elec: PCB v1.1.0 finished
    Still need last checks before ordering.
    [ms-pcb.kicad_pcb, ms-pcb.kicad_sch]
2024-05-06 mec: final prusa slicer files for bumper and caster wheel
    [bumper.3mf, caster-wheel-case.3mf, caster-wheel-spacer.3mf]
2024-05-06 elec: final check for PCB v1.1.0
    Refs: #51
    [ms-pcb.kicad_pcb, ms-pcb.kicad_sch]
2024-05-14 elec: minor changes in PCB
    [ms-pcb.kicad_pcb]
2024-05-17 docs: fix v1.1.0 pin mapping
    [ms-pcb.kicad_pcb, ms-pcb.kicad_sch]
2024-05-24 matlab: script to visualice speed rpm vs command
    [wheelSpeedCalibration1.csv, wheelSpeedCalibration2.csv]
2024-05-27 elec: fix vcc voltage measurement pin
    Closes: #66
    [ms-pcb.kicad_pcb, ms-pcb.kicad_sch]
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2024-05-29 matlab: still working on speed calibration
    [wheelSpeedCalibration3.csv]
2024-06-06 matlab: cpp and matlab correspond for speed calibration
    [polynoms1.csv, wheelSpeedToCommand1.csv]
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2024-06-12 matlab: script to test pid
    [testPid1.csv]
2024-06-14 matlab: test PID results
    [testPid2.csv, testPid3.csv, testPid4.csv]
2024-06-14 docs: more common errors
    [ms-pcb.kicad_sch]
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2024-06-17 matlab: new speed measurement
    [compareSpeeds1.csv, compareSpeeds2.csv, compareSpeeds3.csv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]
2024-06-19 matlab: controller delay impact
    [controllerDelayImpact10ms.csv, controllerDelayImpact1ms.csv, controllerDelayImpact2ms.csv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]
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2024-06-28 pcb: add mouse center point
    [ms-pcb.kicad_pcb]
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2024-07-30 matlab: rework wheel speed plots
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
